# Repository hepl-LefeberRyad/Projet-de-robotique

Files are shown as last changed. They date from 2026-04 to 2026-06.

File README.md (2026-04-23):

# Projet-de-robotique
## Introduction

This repository presents a robotics project developed as part of my Master’s degree program.
<p align="center">

</p>

The project consists of an autonomous robot designed to follow a white line on a black surface. It is equipped with an object detection system that allows it to stop whenever an obstacle is detected in its path.

At the end of the track, the robot uses a robotic arm ,designed in Fusion 360, to push down a figure placed on a platform, and then it turns to return to its starting position.

The robot was programmed using the Arduino IDE, and features a heartbeat LED that reflects its activity through speed-based blinking. An integrated MP3 module also provides audio feedback, announcing the different states and actions of the robot throughout its operation.

## Different Parts

Several components are required to make this project possible. Below are the main elements used in the system.
A schematic diagram is used to illustrate the connections between the Arduino and the different modules.
<p align="center">
BLOCDIAGRAMME drawio
</p>

### Arduino Mega

A microcontroller is necessary to act as the brain of the project. In this case, an Arduino Mega was chosen because it provides a larger number of input/output pins compared to other boards. It can also deliver sufficient current to power multiple connected components through the ATmega2560.
<p align="center">

</p>

https://docs.arduino.cc/hardware/mega-2560/

### Robot chassis

The chassis used for this robot includes integrated motors, but it is unfortunately no longer available on DFROBOT.
<p align="center">

</p>

### MG946R
To make the robot arm move, I used two MG946R servos. These servos are high-torque actuators (up to 13 kg·cm at 6 V) designed for precise positioning and are controlled using PWM signals from the Arduino. One servo is placed at the base of the robot arm to move it forward and backward, while the second servo controls the upper part of the arm, allowing it to move up and down.
<p align="center">

</p>

https://towerpro.com.tw/product/mg946r/
### drv8871

The DRV8871 is a motor driver used to control brushed DC motors by acting as an interface between a microcontroller and the motor, allowing safe handling of higher voltage (6.5 V to 45 V) and current (up to 3.6 A peak). It contains an internal H-bridge made of four N-channel MOSFETs, which enables the motor to rotate in both directions depending on the logic signals applied to the two control pins, IN1 and IN2. The driver supports speed control using PWM (Pulse Width Modulation), where the duty cycle determines the motor speed. It also includes built-in current regulation via the ILIM pin, as well as protection features such as undervoltage lockout, overcurrent protection, and thermal shutdown, ensuring safe and reliable operation. In the robot project, two DRV8871 drivers are used—one for the left motors and one for the right—allowing independent control of each side for movement and steering.

#### IN1 / IN2 Logic Control

- **IN1 = 1, IN2 = 0 → Forward**
  - OUT1 = High, OUT2 = Low  
  - Current flows from OUT1 → OUT2  
  - Motor spins forward  

- **IN1 = 0, IN2 = 1 → Reverse**
  - OUT1 = Low, OUT2 = High  
  - Current flows from OUT2 → OUT1  
  - Motor spins backward  

- **IN1 = 1, IN2 = 1 → Brake (slow decay)**
  - Both outputs are driven LOW  
  - Motor stops quickly (braking effect)  

- **IN1 = 0, IN2 = 0 → Coast / Sleep**
  - Outputs are High-Z (disconnected)  
  - Motor spins freely and gradually stops  
  - Enters low-power sleep mode after ~1 ms  

- **PWM**
  - PWM is applied to one input while the other is kept constant  
  - Example: IN1 = 1 and IN2 = PWM controls forward speed  
  - Higher duty cycle equals to a faster motor speed  
  - Lower duty cycle equals to a slower motor speed
  
<p align="center">

</p>

https://www.ti.com/product/DRV8871

### Qtr MD-01-A

The QTR sensor is an infrared reflectance sensor used to detect differences in surface color or distance. It operates with a voltage between 2.9 V and 5.5 V and outputs an analog voltage between 0 V and VCC depending on how much light is reflected back to the sensor. The sensor works by emitting infrared light and measuring how much of that light is reflected by the surface in front of it. Bright surfaces reflect more light, resulting in a lower output voltage, while dark surfaces reflect less light, resulting in a higher output voltage.

The optimal sensing distance is around 5 mm and each sensor consumes up to 32 mA.

In this project, three QTR sensors are used to detect and follow a line. The sensors are positioned next to each other under the robot:
- The middle sensor is placed above the line (white surface)
- The left and right sensors are placed over the darker background (black surface)

By comparing the values from the three sensors, the robot can determine its position relative to the line:
- If the center sensor detects the line → the robot is correctly aligned
- If the left sensor detects the line → the robot has moved left and needs to correct to the right
- If the right sensor detects the line → the robot has moved right and needs to correct to the left

The analog output of each sensor is read using the Atmega ADC. These values are then used to adjust the motor speeds through the motor drivers, enabling the robot to follow the line smoothly.

The Pololu Arduino library was used to simplify and streamline the coding process.

<p align="center">

</p>
https://www.pololu.com/product/4241

### HC-SR04
The HC-SR04 ultrasonic sensor is used in this project to detect objects in front of the robot and prevent collisions. It works by sending out an ultrasonic sound pulse from the TRIG pin, which travels through the air until it hits an object and is reflected back to the sensor. The ECHO pin measures the time it takes for the sound wave to return. By calculating this time delay, the distance to the object can be determined. In the code, a distance threshold of 8 cm is used; when an object is detected within this range, the robot stops to avoid a collision.
<p align="center">

</p>

### jRQ6500
The JQ6500 is a programmable MP3 module that uses a UART connection with the Arduino Mega to play audio files. In this project, prerecorded sounds are used to indicate the robot’s state; for example, when the robot starts, a voice recording announces “start.”

The library used for controlling the module was downloaded from GitHub. Credit goes to sleemanj and all contributors for making this easy-to-use library available to the public:
https://github.com/sleemanj/JQ6500_Serial
<p align="center">

</p>

https://components101.com/modules/jq6500-mp3-player-module-pinout-features-datasheet-working-application-alternative

### Lipo battery
To power the four DC motors, I used an 11.1 V 3-cell LiPo battery with a capacity of 2200 mAh, which provides sufficient voltage and current to drive the motors through the motor drivers.
<p align="center">

</p>

### 5V powerbank
The other elements of the project are powered by a 5V power bank, which supplies the Arduino Mega, the sensors, the LED, and the MP3 module.
<p align="center">

</p>

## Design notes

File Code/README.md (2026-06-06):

# Introduction
This section contains the main code that was used to make the project work. The robot follows a white line on a black background until all three sensors detect white. Then, the robot uses the robotic arm to push an object. After that, the robot makes a U-turn and follows the line back to the starting line.

The robot is equipped with a heartbeat LED and an MP3 module that announces the start and end of the course. It is also equipped with an ultrasonic sensor to detect objects in its trajectory.

An organigram is also included to provide a better understanding of the structure of the code.

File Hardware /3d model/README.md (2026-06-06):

# Introduction
This section contains the final assembled version of the robotic arm that was developed for the project. The model also includes 3D animations showing the movement of the two axes where the servo motors would be located.

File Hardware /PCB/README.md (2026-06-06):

# Introduction
This section of the repository contains a bill of materials and the schematics I created for a PCB that includes all the different parts.
Altium Designer was used to develop this PCB, and I had to use adapted impedance lines to ensure fast and reliable debugging of the Atmel microcontroller using the FT232.

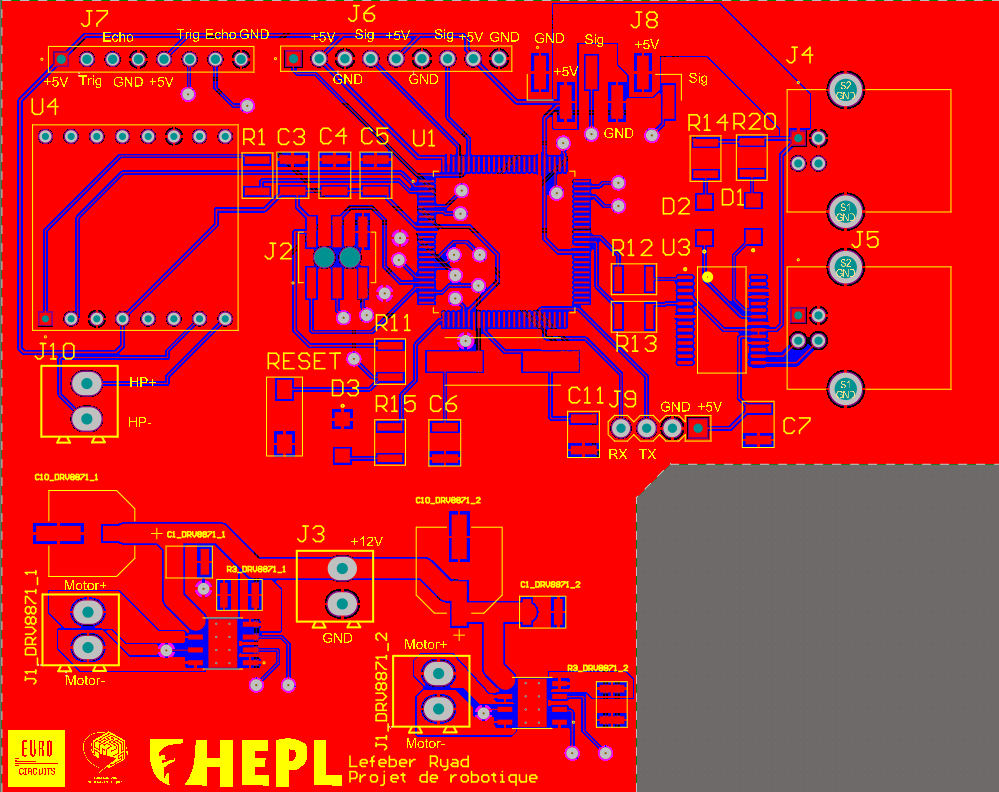
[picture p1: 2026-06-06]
Hardware /PCB/PCB_Projet_robotique.png

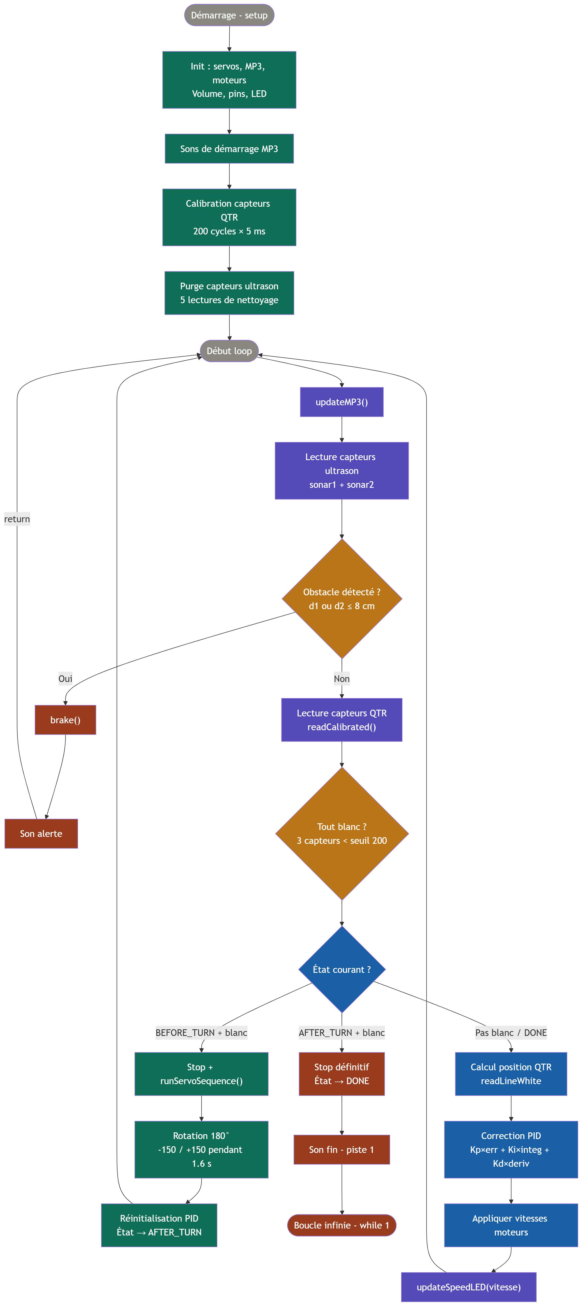
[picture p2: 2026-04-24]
Code/organigramme.png

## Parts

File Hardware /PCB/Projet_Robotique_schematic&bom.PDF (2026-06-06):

Line# | Name | Description | Designator | Revision ID | Revision Status | Quantity | Manufacturer 1 | Manufacturer Part Number 1 | Manufacturer Lifecycle1 | Supplier 1 | Supplier Part Number 1 | Supplier Unit Price1 | Supplier Subtotal 1
| ABLS-16.000MHZ-K4T | HC/49US(AT49) SMDLOW PROFILECRYSTAL | | | | 1 Abracon | | ABLS-16.000MHZ-K4T | VolumeProduction | Mouser | 815-ABLS-16.0M-K4-T | 0,61011 | 0,61011
| 0,1µF | | C1_DRV8871_1, C1_DRV8871_2 | | | 2 KYOCERAAVX | | 04023A101FAT2A | VolumeProduction | Mouser | 581-04023A101F | 0,43825 | 0,8765
| 100nF | | C3, C4, C5, C7 | | | 4 Yageo Group | | C1206C104M5RACTU | VolumeProduction | Farnell | C1206C104M5RACTU | 0,0355 | 0,35497
| 22pF | | C6, C11 | | | 2 Yageo Group | | C1206C220K3HACTU | VolumeProduction | Mouser | 80-C1206C220K3HACTU | 0,1289 | 0,25779
| 22µF | | C10_DRV8871_1, C10_DRV8871_2 | | | 2 Panasonic | | EEE-FN1A220R | VolumeProduction | Mouser | 667-EEE-FN1A220R | 0,34373 | 0,68745
| TXLED | | D1 | | | 1 Lumex | | SML-LX1206YC-TR | VolumeProduction | Mouser | 696-SML-LX1206YC | 0,19764 | 0,19764
| RXLED | | D2 | | | 1 Lumex | | SML-LX1206YC-TR | VolumeProduction | Mouser | 696-SML-LX1206YC | 0,16984 | 0,16984
| 8706943c75ba83719d021d2fd c84c58 | | D3 | | | 1 Lumex | | SML-LX1206YC-TR | VolumeProduction | Mouser | 696-SML-LX1206YC | 0,14594 | 0,14594
| DCMOTOR | | J1_DRV8871_1, J1_DRV8871_2 | | | 2 PhoenixContact | | 1984617 | VolumeProduction | Mouser | 651-1984617 | 0,507 | 1,01
| ICSP | | J2 | | | 1 Samtec | | TMM-103-01-F-D-SM | VolumeProduction | Mouser | 200-TMM10301FDSM | 0,67886 | 0,67886
| Val? | | J3 | | | 1 PhoenixContact | | 1984617 | VolumeProduction | Mouser | 651-1984617 | 0,43567 | 0,43567
| USB5V | USB-B(USBTYPE-B) USB2.0 ReceptacleConnector 4 Position Through Hole, Right Angle | J4 | | | 1 Mill-Max | | 897-43-004-90-000000 | VolumeProduction | Mouser | 575-8974349 | 1,71 | 1,71
| USB-B-S-X-X-TH | USB-B(USBTYPE-B) USB2.0 ReceptacleConnector 4 Position Through Hole, Right Angle | J5 | | | 1 Mill-Max | | 897-43-004-90-000000 | VolumeProduction | Mouser | 575-8974349 | 1,47 | 1,47
| DS1021-1X9SF194-B | 9position 2.54mm singlerow vertical pin header through hole | J6 | | | 1 Wurth Elektronik | | 61300911121 | VolumeProduction | DigiKey | 732-5322-ND | 0,3781 | 0,3781
| MTSW-108-24-G-S-245 | Connector Header Through Hole8position 0.100 (2.54mm) | J7 | | | 1 Samtec | | MTSW-108-24-G-S-245 | VolumeProduction | Avnet | MTSW-108-24-G-S-245 | 0,77476 | 0,77476
| TSM-106-03-T-SV | Conn Unshrouded Header HDR6POS2.54mm Solder ST SMDTube | J8 | | | 1 Samtec | | TSM-106-03-T-SV | VolumeProduction | Mouser | 200-TSM10603TSV | 0,61011 | 0,61011

HC-05

RECEPTACLE, 2.54MM, SINGLE, 4WAY; Pitch Spacing:2.54mm; No. of Contacts:4Contacts; Gender:Receptacle; Product Range:SSQSeries; Contact
Termination Type:Through
Hole; No. of Rows:1Rows;
Contact Plating:Gold Plated Contacts; Contact
Material:Phosphor Bronze;
SVHC:No SVHC(15-Jan-2018); Colour:Black; Contact
Resistance:10mohm; Contact Termination:Through Hole
Vertical; Lead
Spacing:2.54mm; Operating
Temperature Max:125Â°C;
OperatingTemperature Min:-55Â°C; Termination
Method:Solder; Voltage
RatingVAC:550V
J9 | 1 Sullins | LPPB041NFFN-RC | VolumeProduction | DigiKey | S9008E-04-ND | 0,66167 | 0,66167
Speaker | | J10 | 1 PhoenixContact | 1984617 | VolumeProduction | Mouser | 651-1984617 | 0,37438 | 0,37438
1K | | R1 | 1 Vishay | MCA1206MD1001BP100 | VolumeProduction | Mouser | 594-MCA1206MD1001BP1 | 0,97962 | 0,97962
30K | | R3_DRV8871_1, R3_DRV8871_2 | 2 ROHM | ESR18EZPF3002 | VolumeProduction | Mouser | 755-ESR18EZPF3002 | 0,15468 | 0,30935
10k | | R11 | 1 Yageo Group | YC324-JK-0710KL | VolumeProduction | Mouser | 603-YC324-JK-0710KL | 0,23201 | 0,23201
1k | | R12, R13 | 2 Vishay | MCA1206MD1001BP100 | VolumeProduction | Mouser | 594-MCA1206MD1001BP1 | 0,8418 | 1,68
270 | | R14, R15, R20 | 3 Vishay | CRCW1206270RJNEA | VolumeProduction | Avnet | 59M6975 | 0,01719 | 0,05156
DTSM-32S-B | | RESET | 1 ALPS | SKSTAAE010 | VolumeProduction | DigiKey | 4809-SKSTAAE010CT-ND | 1,09 | 1,09
ATmega2560-16AU | | U1 | 1 Microchip | ATMEGA256016AU | VolumeProduction | Farnell | ATMEGA2560-16AU | 18,56 | 18,56
DRV8871DDA | 50-V, 3.6-AH-bridgemotor driver with integrated current sensing | U2_DRV8871_1, U2_DRV8871_2 | 2 Texas Instruments | DRV8871DDARQ1 | VolumeProduction | Mouser | 595-DRV8871DDARQ1 | 3,39 | 6,77
FTDI-FT232-SSOP-28 | | U3 | 1 Futuretech | FT232RNL-REEL | VolumeProduction

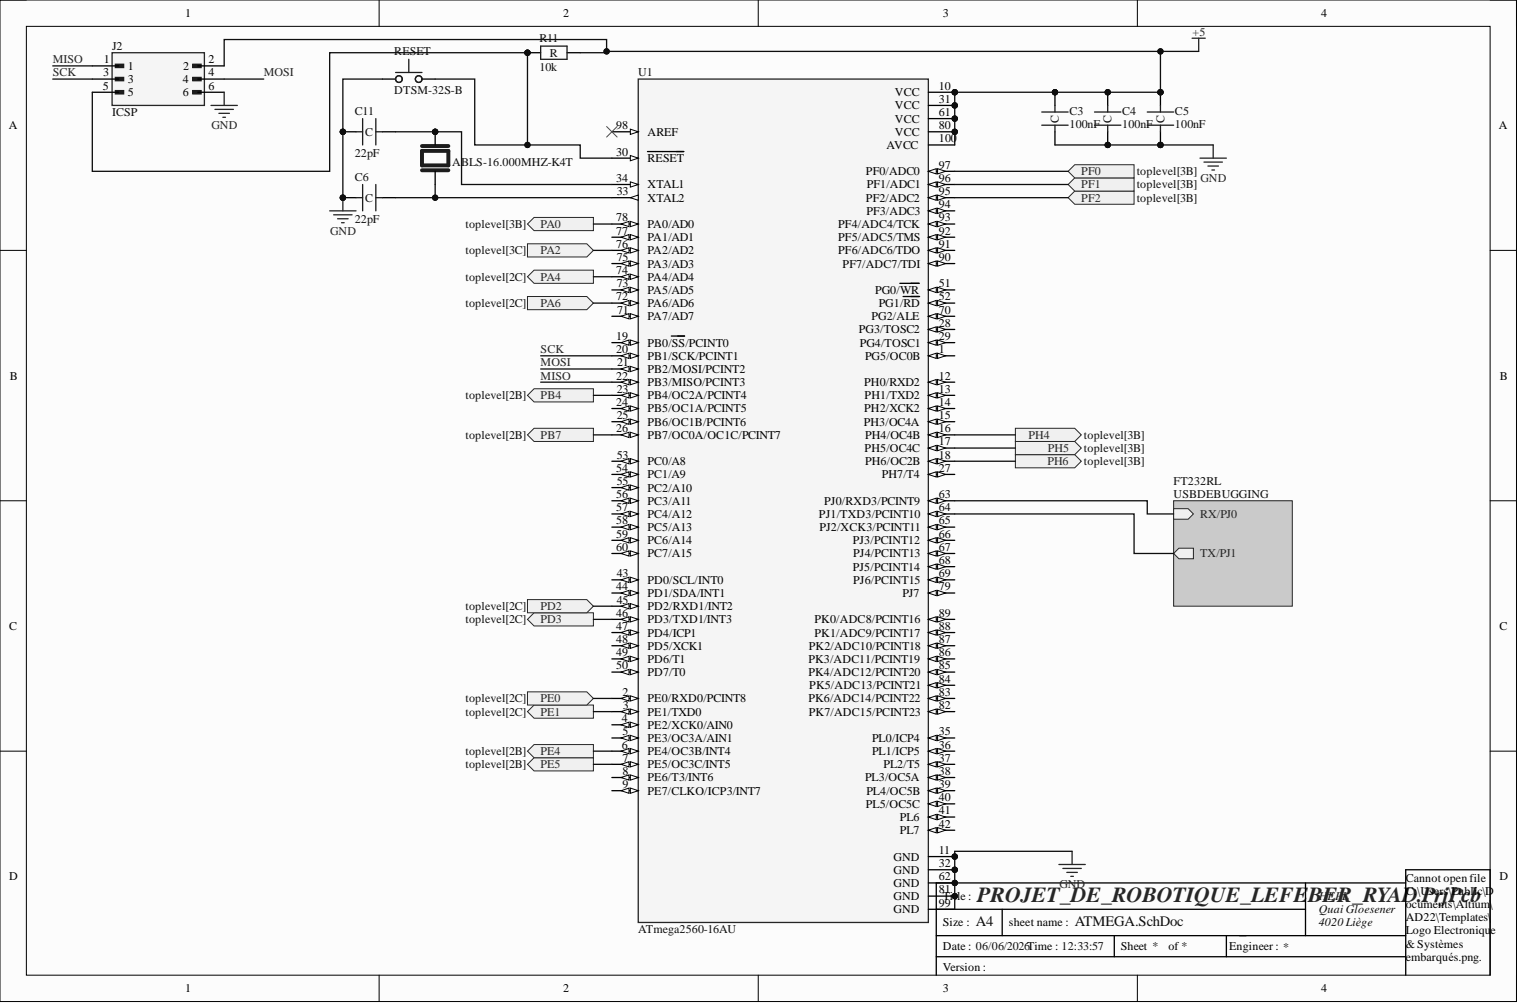
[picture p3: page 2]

Title : | PROJET_DE_ROBOTIQUE_LEFEBER_RYAD.PrjPcb | HEPL Quai Gloesener 4020 Liège

Size : A4 | sheet name : ATMEGA.SchDoc

Date : 06/06/2026 Time : 12:33:57 | Sheet * of | Engineer :

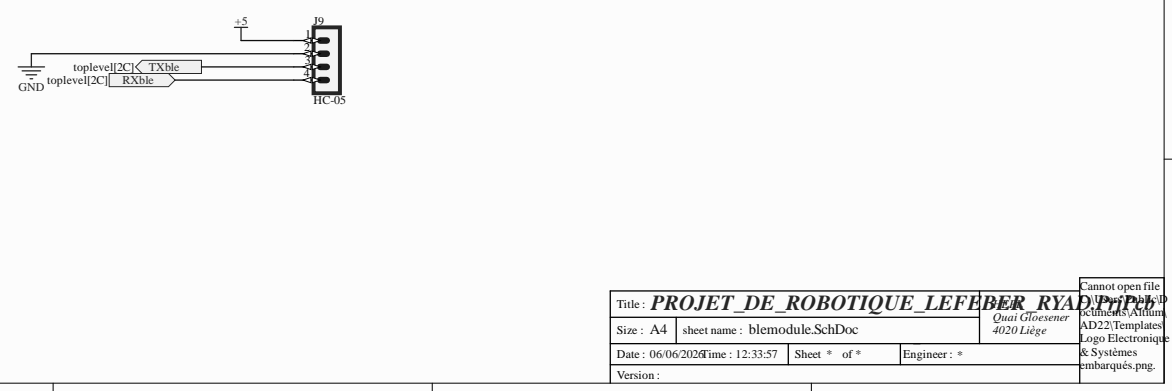
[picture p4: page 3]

PROJET_DE_ROBOTIQUE_LEFEBER_RYAD.PrjPcb Title : | HEPL Quai Gloesener

blemodule.SchDoc

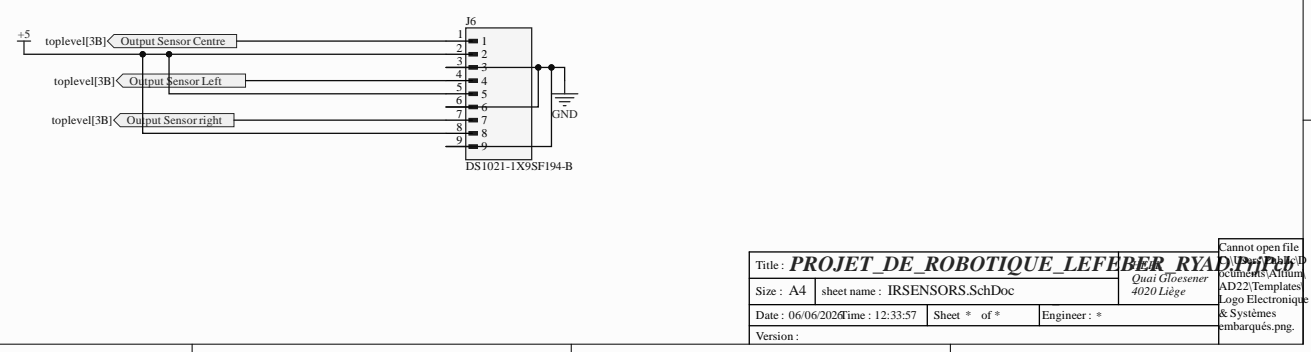
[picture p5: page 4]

PROJET_DE_ROBOTIQUE_LEFEBER_RYAD.PrjPcb Title : | HEPL Quai Gloesener

IRSENSORS.SchDoc

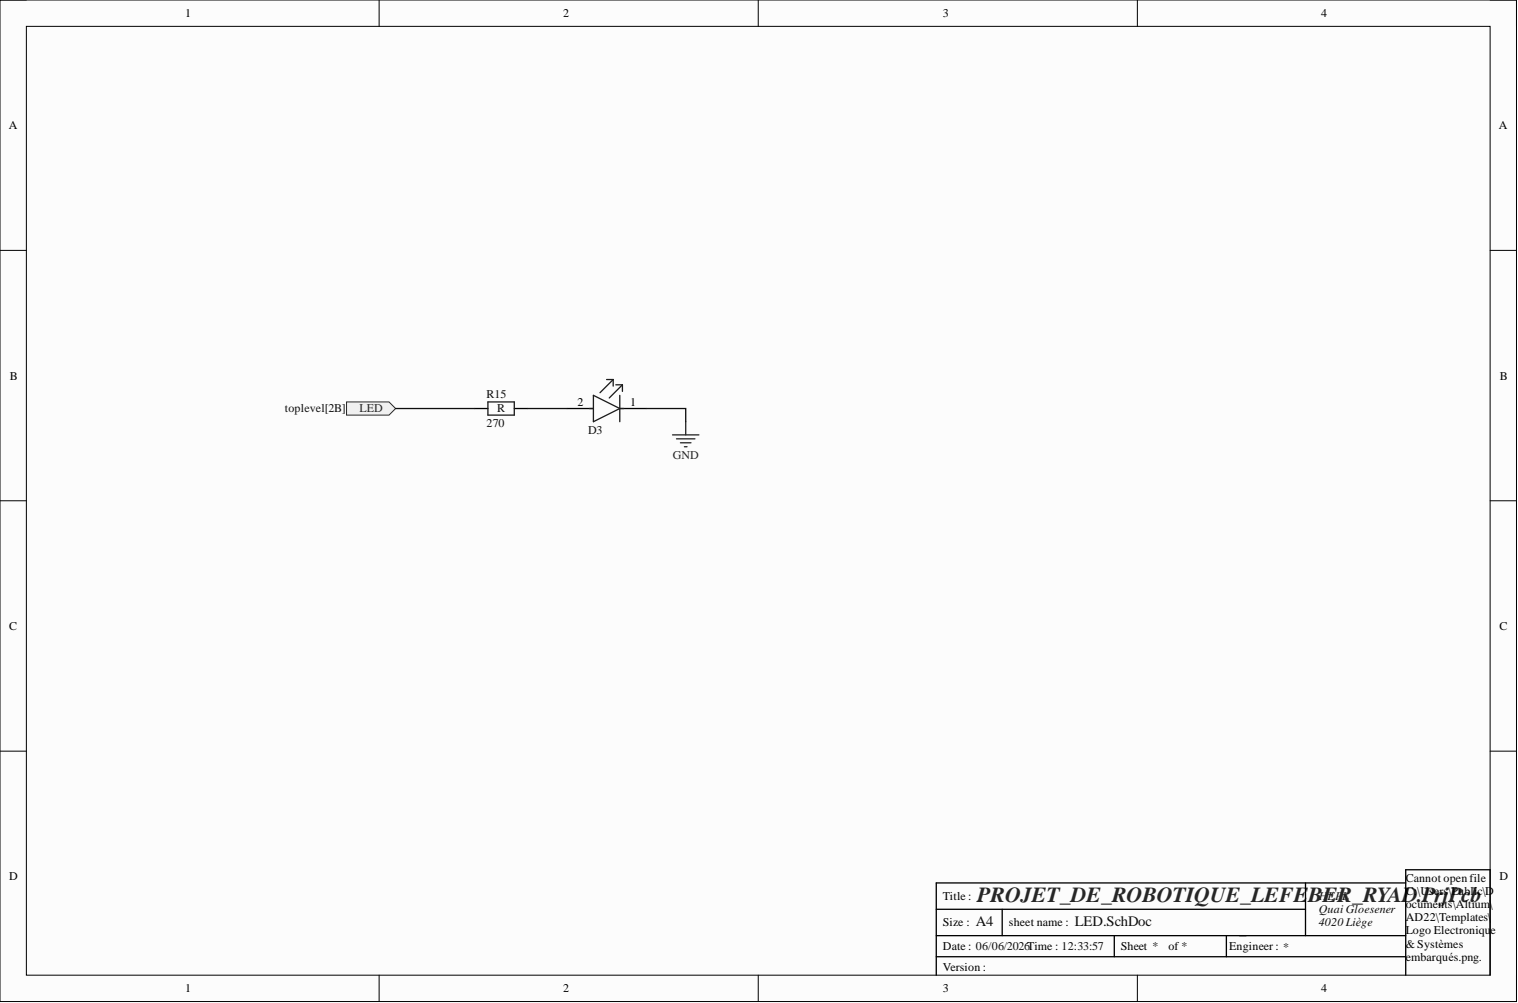
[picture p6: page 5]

PROJET_DE_ROBOTIQUE_LEFEBER_RYAD.PrjPcb Title : | HEPL Quai Gloesener

LED.SchDoc

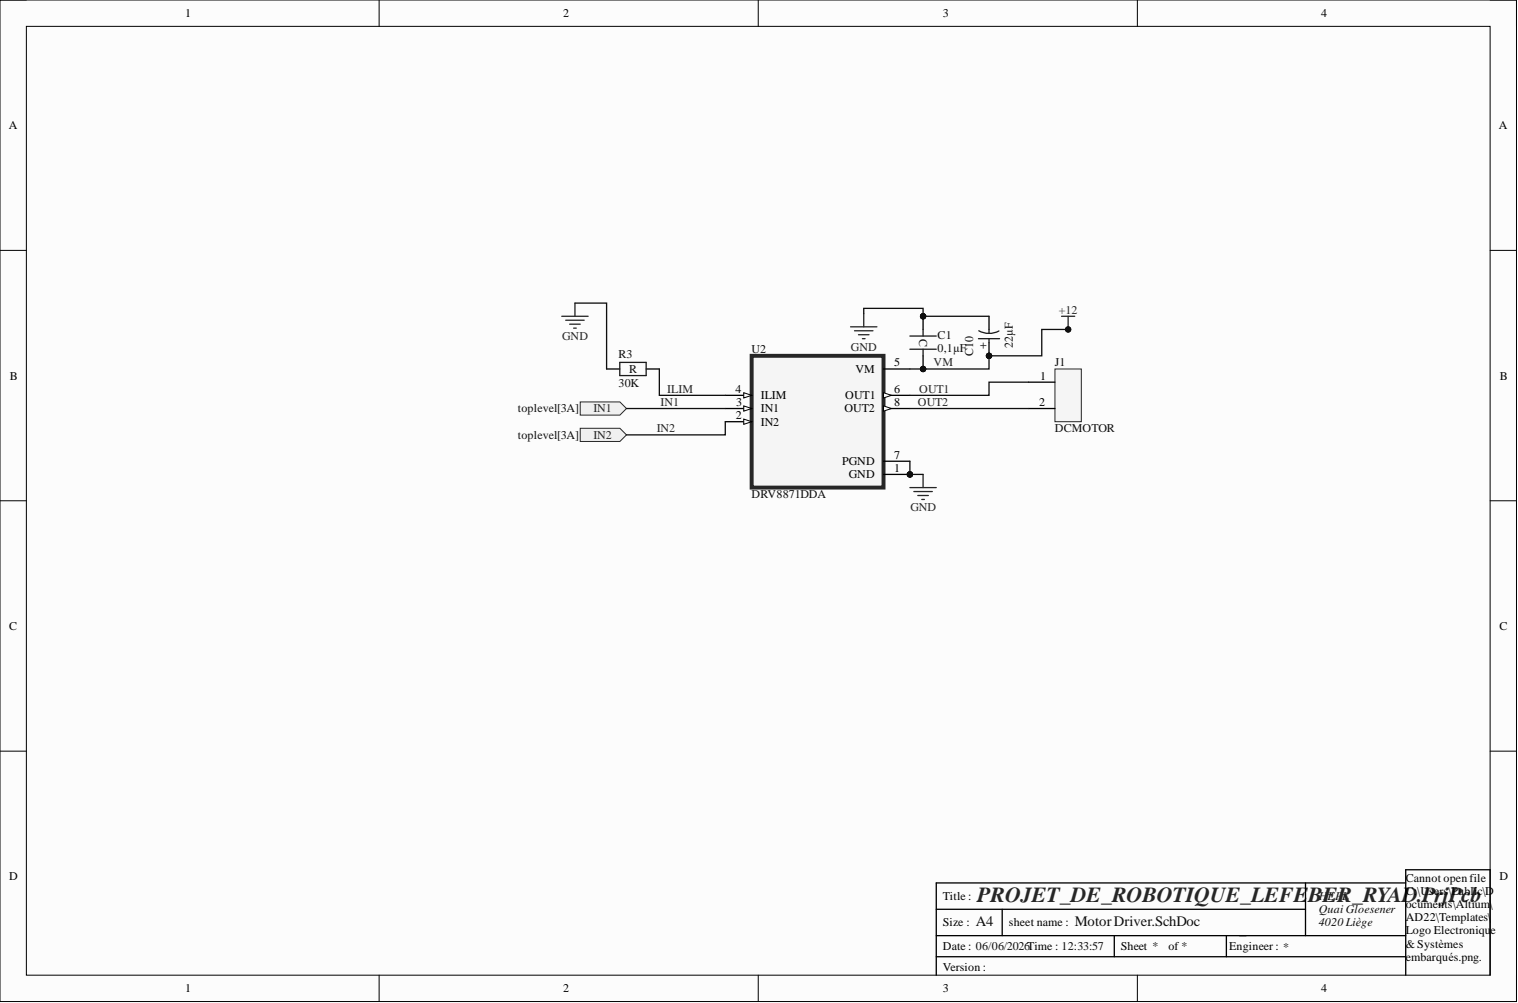
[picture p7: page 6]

PROJET_DE_ROBOTIQUE_LEFEBER_R T i t le : | YA HEPL Quai G l oesen e r 0 Li è g e

Size : A | s heet name : M otor Driv e r.S c h D o c

Date : / / T ime : : : | Shee t o f | E n g i neer :

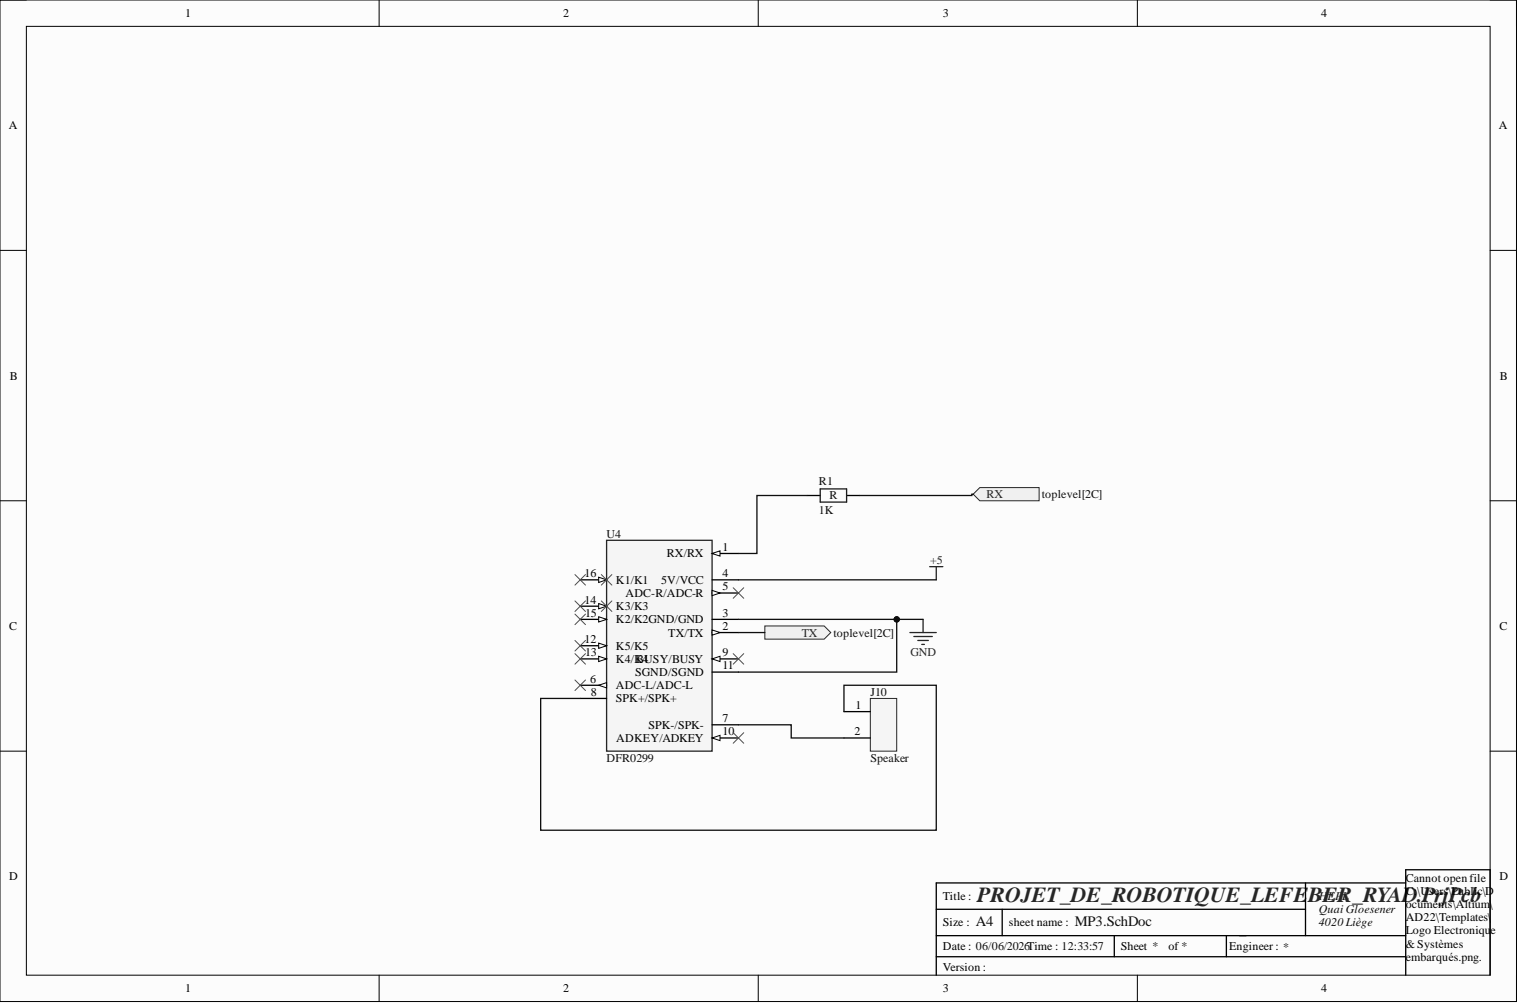
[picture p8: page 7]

PROJET_DE_ROBOTIQUE_LEFEBER_RYAD.PrjPcb Title : | HEPL Quai Gloesener

MP3.SchDoc

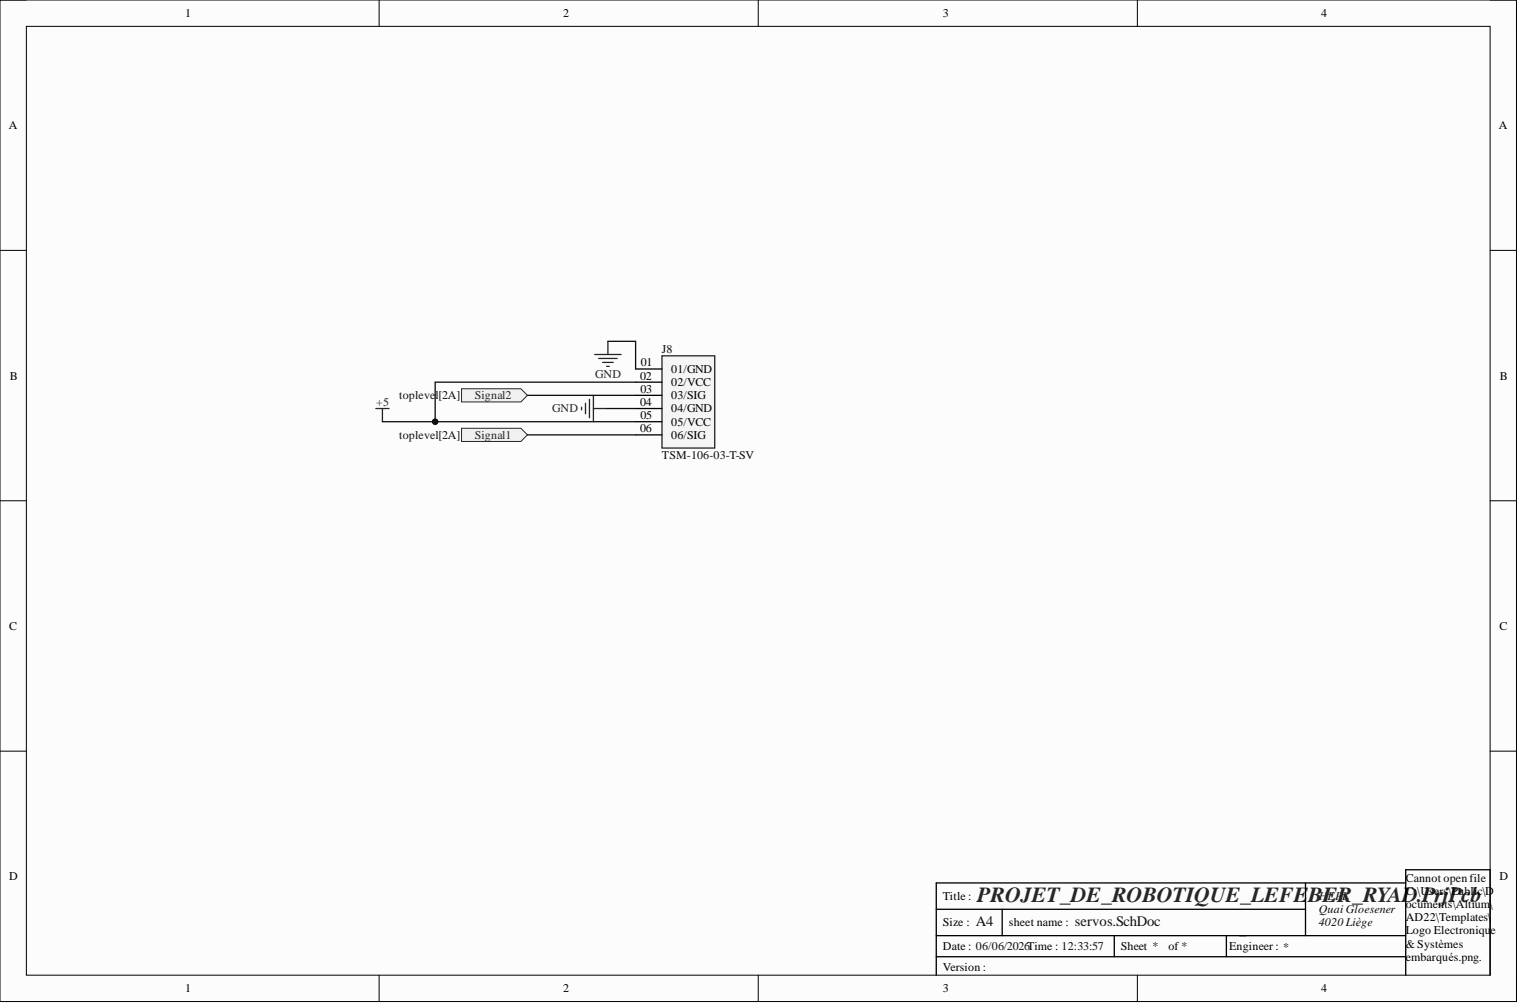
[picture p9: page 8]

PROJET_DE_ROBOTIQUE_LEFEBER_RYAD.PrjPcb Title : | HEPL Quai Gloesener

servos.SchDoc

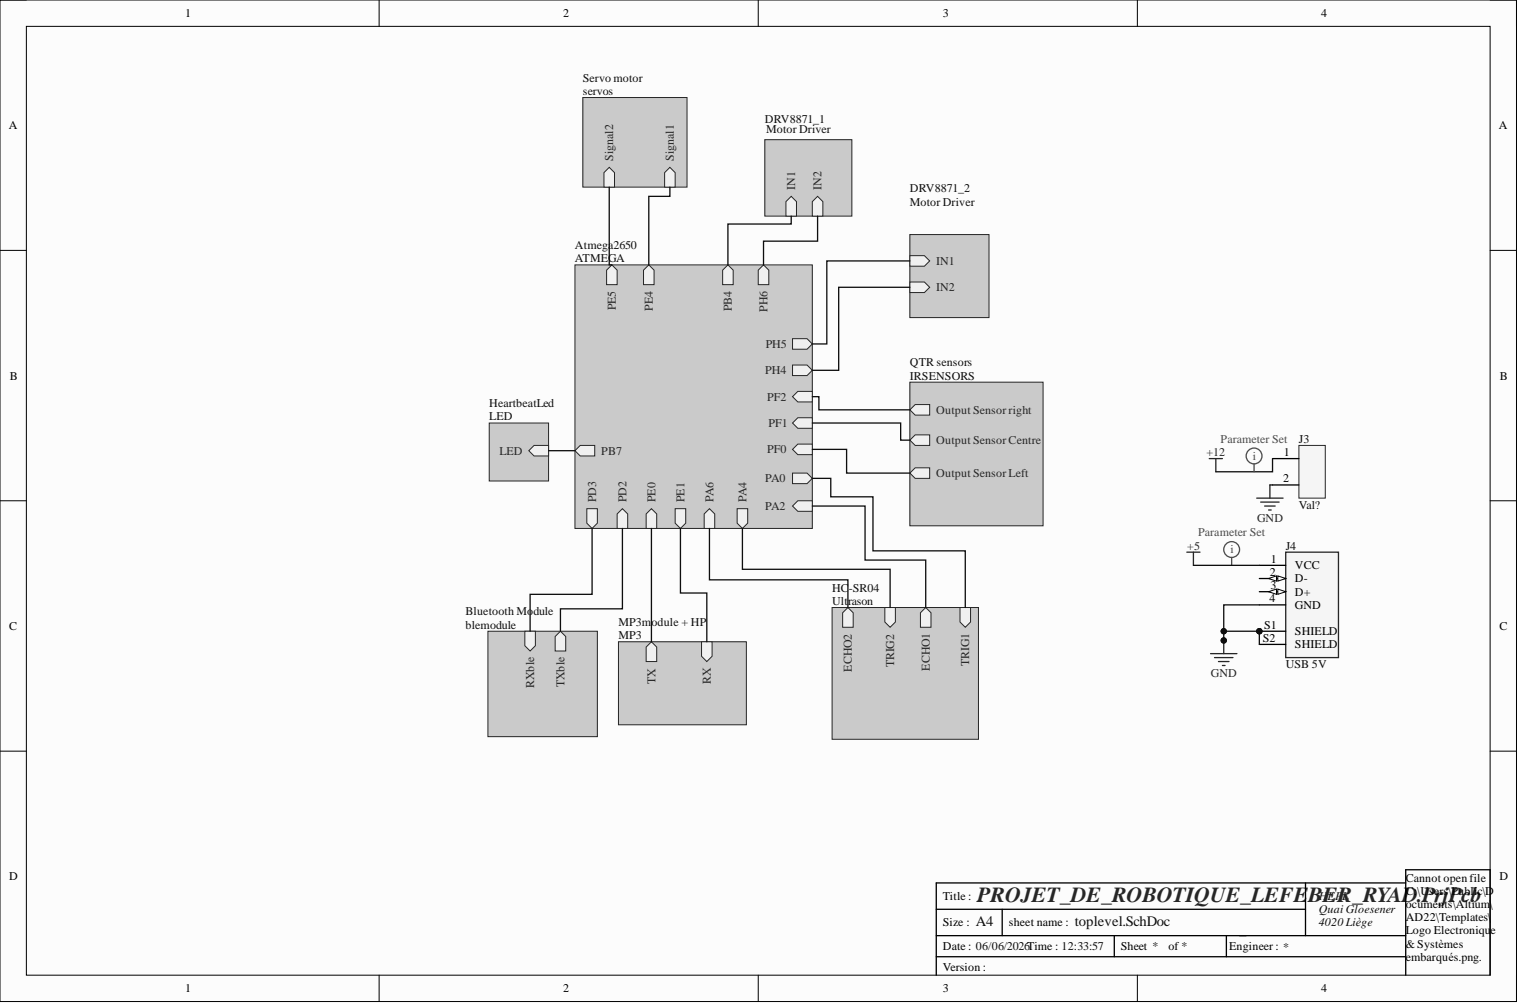
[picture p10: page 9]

HC-SR04 Ultrason

SHIELD S1

PROJET_DE_ROBOTIQUE_LEFEBER_RYAD.PrjPcb Title : | HEPL Quai Gloesener

toplevel.SchDoc


t o p level [ 3 C ] TRIG 1 | 0 2 0 3 0 4

PROJET_DE_ROBOTIQUE_LEFEBER_R T i t le : | YA HEPL Quai G l oesen e r 0 Li è g e

Size : A | s heet name : Ultraso n . S c h D o c

Date : / / T ime : : : | Shee t o f | E n g i neer :


PROJET_DE_ROBOTIQUE_LEFEBER_R T i t le : | YA HEPL Quai G l oesen e r 0 Li è g e

Size : A | s heet name : USBDEBUGGING . S c h D o c

Date : / / T ime : : : | Shee t o f | E n g i neer :

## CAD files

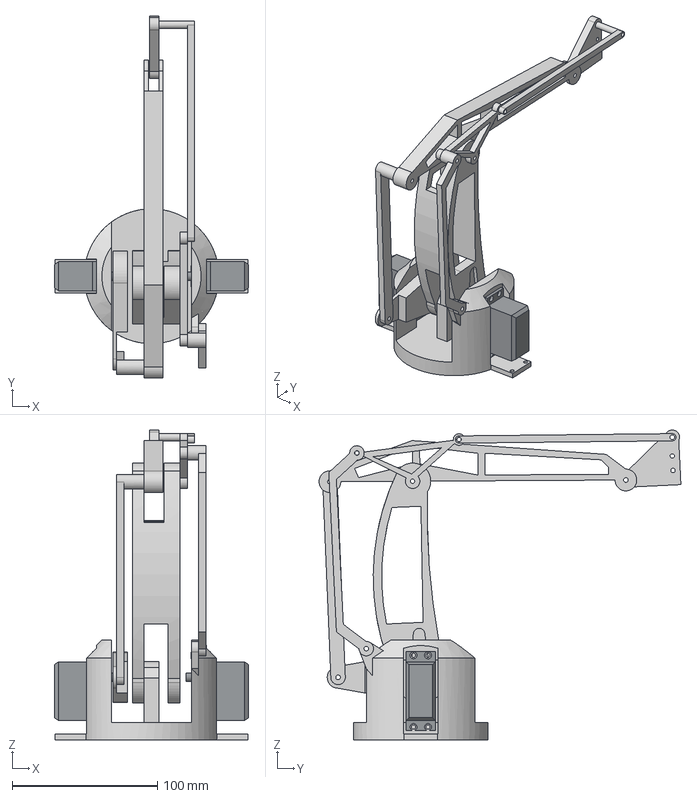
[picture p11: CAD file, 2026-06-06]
Hardware /3d model/Assemblage.step
134.0 x 249.4 x 213.7 mm
socle
MG946R x 2
Bras_principal_Ryad
pièce_servo2
pieceduhaut
PIECESUPPORTARRIEREFINE
pièce_arrière
ngle
PIECEPUNCH_1
support_haut

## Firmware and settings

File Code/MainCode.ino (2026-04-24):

#include <QTRSensors.h>          // Library for line sensors
#include <NewPing.h>             // Library for ultrasonic sensors
#include <JQ6500_Serial.h>       // Library for MP3 module
#include <Servo.h>               // Library for servo motors

const int PIN_SERVO_1 = 11;      // Pin for servo 1
const int PIN_SERVO_2 = 12;      // Pin for servo 2

Servo servo1;                    // Create servo 1 object
Servo servo2;                    // Create servo 2 object

QTRSensors qtr;                  // Create QTR sensor object

const uint8_t SensorCount = 3;   // Number of line sensors
uint16_t sensorValues[3];        // Array to store sensor readings

// millis
unsigned long mp3Timer = 0;      // Timer for MP3 playback
bool mp3Busy = false;            // Indicates if MP3 is playing
uint16_t currentTrack = 0;       // Current track number
unsigned long mp3Duration = 0;   // Duration of current track

// --- Speed-based blinking LED ---
#define LED_PIN 13               // LED pin
unsigned long ledTimer = 0;      // Timer for LED blinking
bool ledState = false;           // LED ON/OFF state
unsigned long blinkInterval = 500; // Blink interval in ms

// Motor pins
#define IN1L 5                   // Left motor pin 1
#define IN2L 6                   // Left motor pin 2
#define IN1R 9                   // Right motor pin 1
#define IN2R 10                  // Right motor pin 2
#define WHITE_THRESHOLD 200      // Threshold to detect white surface

bool audioPlayed = false;        // Prevents repeated audio playback

int baseSpeed = 65;              // Base speed of robot
int maxSpeed = 255;              // Maximum motor speed

// PID constants
float Kp = 0.2;                 // Proportional gain
float Ki = 0.0;                 // Integral gain
float Kd = 0.41;                // Derivative gain

int lastError = 0;              // Previous error value
int integral = 0;               // Integral sum

unsigned long turnDelay = 1600; // Duration for 180° turn

enum RobotState {               // Robot states
  BEFORE_TURN,                 // Before first white line
  AFTER_TURN,                  // After turning
  DONE                         // Finished state
};

RobotState state = BEFORE_TURN; // Initial state

// --- Ultrasonic sensors ---
#define TRIG1 22                // Trigger pin sensor 1
#define ECHO1 24                // Echo pin sensor 1
#define TRIG2 26                // Trigger pin sensor 2
#define ECHO2 28                // Echo pin sensor 2
#define MAX_DISTANCE 30         // Max detection distance (cm)
#define SEUIL_OBJET 8           // Object detection threshold

NewPing sonar1(TRIG1, ECHO1, MAX_DISTANCE); // Ultrasonic sensor 1
NewPing sonar2(TRIG2, ECHO2, MAX_DISTANCE); // Ultrasonic sensor 2

JQ6500_Serial mp3(Serial1);     // MP3 module on Serial1

void setup() {
  Serial.begin(9600);          // Start serial communication
  Serial1.begin(9600);         // Start MP3 serial communication

  servo1.attach(PIN_SERVO_1);  // Attach servo 1
  servo2.attach(PIN_SERVO_2);  // Attach servo 2

  servo1.write(130);           // Set initial position servo 1
  delay(500);                  // Wait 500 ms

  servo2.write(40);            // Set initial position servo 2
  delay(500);                  // Wait 500 ms

  mp3.setVolume(30);           // Set MP3 volume

  qtr.setTypeAnalog();         // Set sensors to analog mode
  qtr.setSensorPins((const uint8_t[]){A0, A1, A2}, 3); // Define sensor pins

  pinMode(IN1L, OUTPUT);       // Set motor pins as output
  pinMode(IN2L, OUTPUT);
  pinMode(IN1R, OUTPUT);
  pinMode(IN2R, OUTPUT);
  pinMode(LED_PIN, OUTPUT);    // Set LED pin as output

  delay(500);                  // Wait before starting

  playMP3_blocking(7, 3000);   // Play startup sound
  playMP3_blocking(3, 2000);
  playMP3_blocking(4, 2000);

  Serial.println("Calibrating..."); // Print calibration message
  for (int i = 0; i < 200; i++) {   // Calibration loop
    qtr.calibrate();                // Calibrate sensors
    delay(5);                       // Small delay
  }

  playMP3_blocking(5, 2000);  // Play calibration done sound
  Serial.println("Done!");    // Print done message

  delay(100);                // Wait before ultrasonic purge
  for (int i = 0; i < 5; i++) { // Clean sensor readings
    sonar1.ping_cm();           // Read sensor 1
    sonar2.ping_cm();           // Read sensor 2
    delay(30);                  // Small delay
  }
  delay(200);                 // Final delay
}

void runServoSequence() {
  servo1.write(160);         // Move servo 1
  delay(1500);               // Wait

  servo2.write(80);          // Move servo 2
  delay(1500);

  servo2.write(20);          // Move servo 2 again
  delay(1500);

  servo1.write(130);         // Reset servo 1
  delay(1500);
}

// --- LED blink based on speed ---
void updateSpeedLED(int speed) {
  speed = constrain(abs(speed), 0, maxSpeed); // Normalize speed

  if (speed < 10) {           // If almost stopped
    digitalWrite(LED_PIN, HIGH); // Keep LED ON
    return;                   // Exit function
  }

  blinkInterval = map(speed, 10, maxSpeed, 800, 100); // Adjust blink speed

  if (millis() - ledTimer >= blinkInterval) { // Check timing
    ledTimer = millis();       // Reset timer
    ledState = !ledState;      // Toggle LED state
    digitalWrite(LED_PIN, ledState); // Apply state
  }
}

void setMotor(int leftSpeed, int rightSpeed) {
  leftSpeed = constrain(leftSpeed, -maxSpeed, maxSpeed); // Limit speed
  rightSpeed = constrain(rightSpeed, -maxSpeed, maxSpeed);

  if (leftSpeed >= 0) {       // Forward left motor
    analogWrite(IN1L, leftSpeed);
    analogWrite(IN2L, 0);
  } else {                    // Reverse left motor
    analogWrite(IN1L, 0);
    analogWrite(IN2L, -leftSpeed);
  }

  if (rightSpeed >= 0) {      // Forward right motor
    analogWrite(IN1R, rightSpeed);
    analogWrite(IN2R, 0);
  } else {                    // Reverse right motor
    analogWrite(IN1R, 0);
    analogWrite(IN2R, -rightSpeed);
  }
}

void brake() {
  analogWrite(IN1L, 255);     // Apply brake left motor
  analogWrite(IN2L, 255);
  analogWrite(IN1R, 255);     // Apply brake right motor
  analogWrite(IN2R, 255);
}

void playMP3_blocking(uint16_t track, unsigned long duration) {
  mp3.playFileByIndexNumber(track); // Play track
  delay(duration);                  // Wait until finished
}

void playMP3_nonBlocking(uint16_t track, unsigned long duration) {
  if (!mp3Busy || (millis() - mp3Timer > mp3Duration - 100)) { // Check availability
    mp3.playFileByIndexNumber(track); // Play track
    currentTrack = track;             // Save track
    mp3Duration = duration;           // Save duration
    mp3Timer = millis();              // Start timer
    mp3Busy = true;                  // Set busy flag
  }
}

void updateMP3() {
  if (mp3Busy && (millis() - mp3Timer >= mp3Duration)) { // Check if done
    mp3Busy = false;            // Reset flag
  }
}

void loop() {
  updateMP3();                 // Update MP3 state

  unsigned int d1 = sonar1.ping_cm(); // Read distance sensor 1
  delay(15);                          // Small delay
  unsigned int d2 = sonar2.ping_cm(); // Read distance sensor 2

  if ((d1 > 0 && d1 <= SEUIL_OBJET) || (d2 > 0 && d2 <= SEUIL_OBJET)) { // Object detected
    brake();                          // Stop robot
    Serial.println("Object detected, braking!"); // Debug message
    delay(50);                        // Short delay

    updateSpeedLED(0);                // Update LED

    if (!audioPlayed) {               // Play sound once
      playMP3_nonBlocking(8, 2000);
      audioPlayed = true;
    }

    return;                           // Skip rest of loop
  }

  audioPlayed = false;                // Reset audio flag

  qtr.readCalibrated(sensorValues);  // Read line sensors

  bool allWhite =                   // Check if all sensors see white
    sensorValues[0] < WHITE_THRESHOLD &&
    sensorValues[1] < WHITE_THRESHOLD &&
    sensorValues[2] < WHITE_THRESHOLD;

  if (state == BEFORE_TURN && allWhite) { // First white line
    Serial.println("STOP - First white detected");

    brake();                       // Stop robot
    updateSpeedLED(0);            // Update LED
    runServoSequence();           // Run servo animation

    Serial.println("Turning 180 degrees");
    setMotor(-150, 150);          // Rotate robot
    delay(turnDelay);             // Wait for turn

    brake();                      // Stop again
    delay(200);

    integral = 0;                 // Reset PID
    lastError = 0;

    state = AFTER_TURN;           // Change state
  }
  else if (state == AFTER_TURN && allWhite) { // Second white line
    Serial.println("STOP - Second white detected, finished");

    brake();                      // Stop robot
    updateSpeedLED(0);

    state = DONE;                 // Final state
    playMP3_nonBlocking(1, 2000); // Play finish sound

    while (1) {                   // Infinite stop loop
      updateSpeedLED(0);
    }
  }

  if (state != DONE) {            // If still running
    uint16_t position = qtr.readLineWhite(sensorValues); // Get position

    int error = position - 1000;  // Compute error

    integral += error;            // Update integral
    int derivative = error - lastError; // Compute derivative

    int correction = Kp * error + Ki * integral + Kd * derivative; // PID
    lastError = error;            // Save error

    int leftSpeed = baseSpeed + correction;  // Adjust left speed
    int rightSpeed = baseSpeed - correction; // Adjust right speed

    setMotor(leftSpeed, rightSpeed); // Apply speeds

    int currentSpeed = (abs(leftSpeed) + abs(rightSpeed)) / 2; // Average speed
    updateSpeedLED(currentSpeed);   // Update LED

    Serial.print("Pos: ");         // Debug output
    Serial.print(position);
    Serial.print(" Error: ");
    Serial.println(error);
  }
}
